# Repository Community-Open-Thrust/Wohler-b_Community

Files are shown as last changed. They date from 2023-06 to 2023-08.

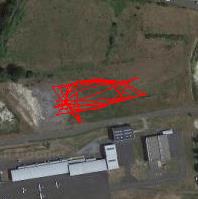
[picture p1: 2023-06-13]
Flight_Tests/logs from 03-17 to 03-24/2019-03-17 19-36-37.bin.jpg

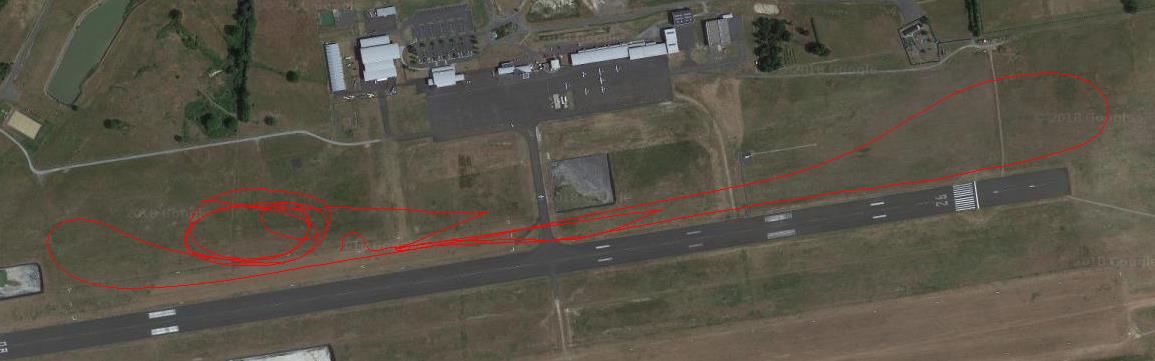
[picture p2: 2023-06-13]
Flight_Tests/logs from 03-17 to 03-24/2019-03-21 13-17-54.log.jpg

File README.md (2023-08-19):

# Wohler-b transport turbo-drone - Community Edition

This is the repository for the Community Edition Release of the community of makers from Neva Aerospace Ltd (UK) for the turbo-drone Wohler-b series for transporation.



Wohler-b series can be used with Athena-A-2ET (2stages) or Athena-A-1ET (1 stage) electric turbines (Electric Ducted Fans (EDF))

# THE LICENCE IS CERN-OHL-S (Strongly Reciprocal) 
https://ohwr.org/cern_ohl_s_v2.pdf


Any further fork and/or modification must bear the following Notice as per chapter 1.10 of Definition of the OHL-s :
"Acknowledgement of the Original Authors: Neva-Aero and the Human Team Members between 2013 and 2022 : F.M. Robert Vergnes, David Brotherton-Ratcliffe, Aleksey Zaitsevsky, Renaud-Pierre Blanpain, Anthony Gambus, Tal Stokes, Valentin Bertrand, Tomas Valaitis, Louis Fourdan, Elie de Fonclare, Frédéric Pudleitner, Gilles Coïa  "

# About using this repository
MAIN WILL NOT CHANGE.
The main of repository will be locked to the initial commit to avoid losing information. 
Please do create a new branch for a new version or create your own fork.
Please check the branch for the early or the last version of the project.

# Serialisation & History
It started in 2016-2017 with the Eole X4, followed by the Wohler-b-III-x4 (Mark 3) and then the Wohler-b-Mark-V-X8 (Wohler b mark 5).

The Eole-X4 was used for demonstration in Oct. 2017 with Thales for the French Army (STAT) at Satory Camp (France) and the Eole-X4 was then presented at the Paris Air Show 2017 at the PAS-Start-up-Aero-LAB. It ended its life at the Aero-Museum of Angers Airport. 

The Wohler-b-III-x4 (mark3) had a short life from 2017 to 2018 and the fate of the last prototype is unkown.

The Wohler-b-Mark-V-X12 (Mark5) was built between 2018 and 2019 and used for several demonstrations, among which for the French Army (STAT) were BVLOS was demonstrated using 4G and the FlyTbase cloud and UAVCast for delivery of 3Kg to 5kg package. The Wohler-b-Mark-V-X12 was presented to the Paris Air Show 2019 and the late Olivier Dassault, MP & Pilot, came to congratulates the team for the technological advance. The prototype has been dismantled at the closure of the Angers Airport operations in France.

There has been some sketches and early draft for the Wohler-D and the Wohler-b-Mark-VI-x12 but they have never been built.

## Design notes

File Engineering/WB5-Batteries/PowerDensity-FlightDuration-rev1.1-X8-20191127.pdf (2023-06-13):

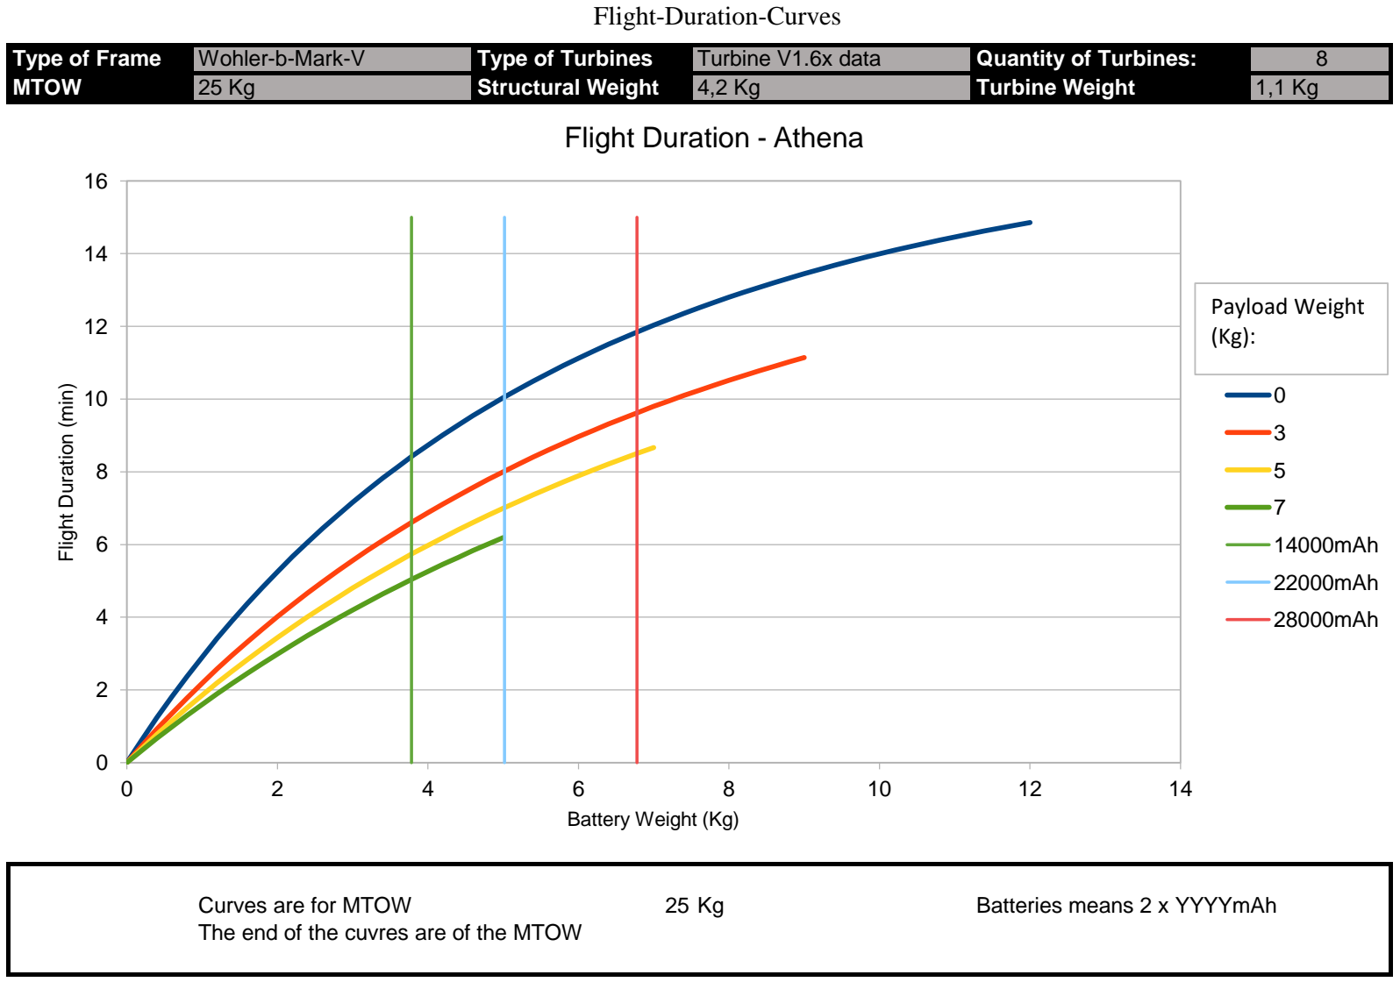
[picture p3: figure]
Flight-Duration-Curves; MTOW 25 Kg; Structural Weight 4,2 Kg; Turbine Weight 1,1 Kg; Curves are for MTOW; Batteries means 2 x YYYYmAh; The end of the cuvres are of the MTOW; Flight Duration (min); Battery Weight (Kg); Flight Duration - Athena; 14000mAh; 22000mAh; 28000mAh; Payload Weight (Kg):

Type of Frame Wohler-b-Mark-V | Type of Turbines Turbine V1.6x data | Quantity of Turbines: 8

Page 1

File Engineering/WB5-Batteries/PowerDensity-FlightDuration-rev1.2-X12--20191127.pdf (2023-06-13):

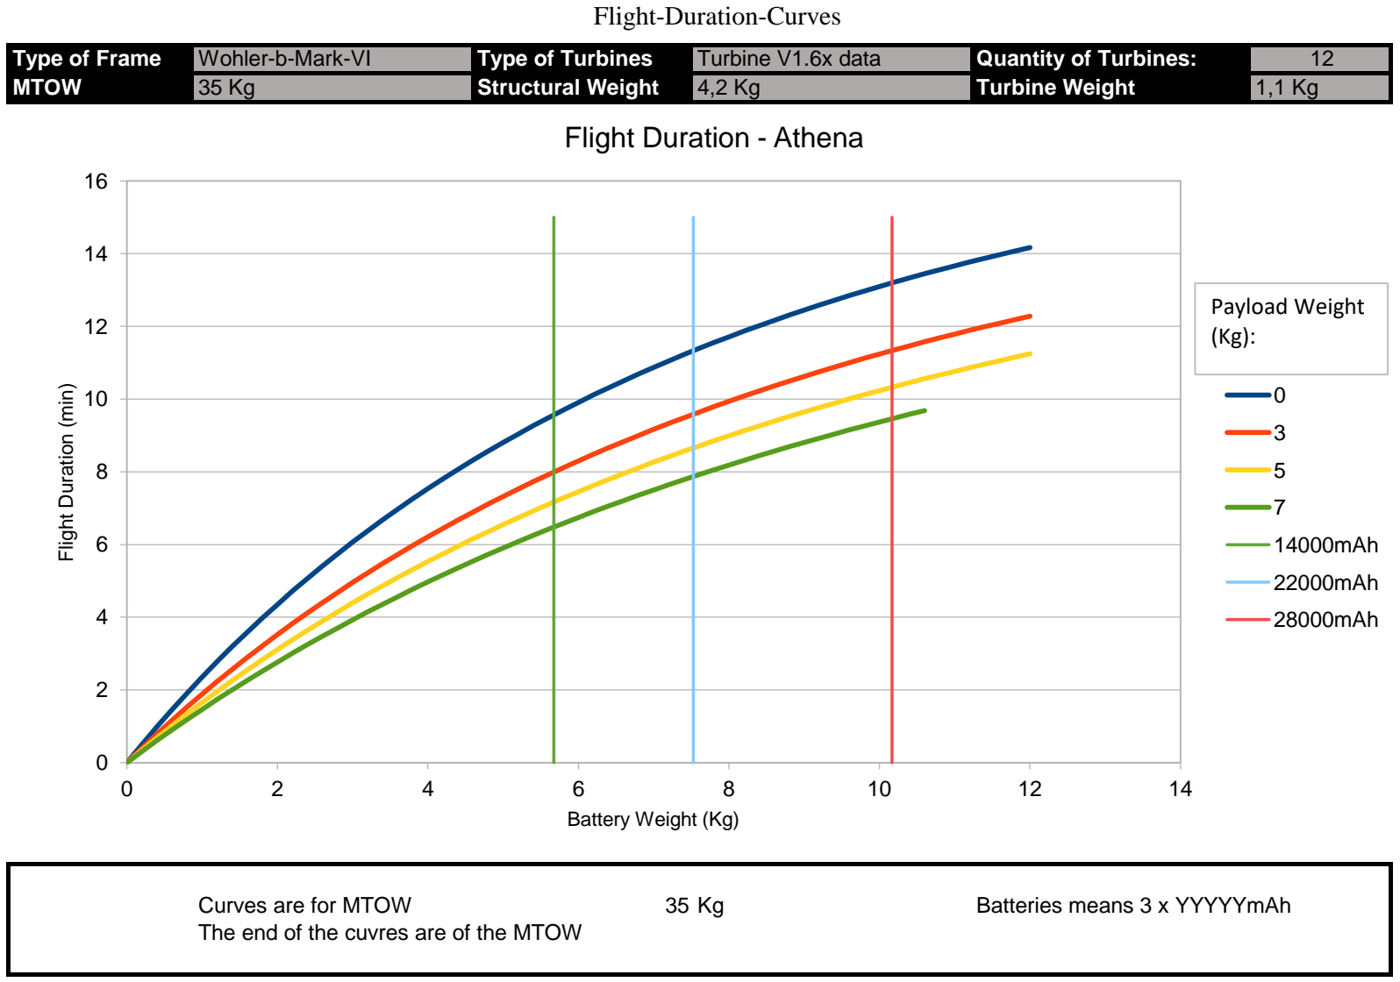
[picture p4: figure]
Flight-Duration-Curves; MTOW 35 Kg; Structural Weight 4,2 Kg; Turbine Weight 1,1 Kg; Curves are for MTOW; Batteries means 3 x YYYYYmAh; The end of the cuvres are of the MTOW; Flight Duration (min); Battery Weight (Kg); Flight Duration - Athena; 14000mAh; 22000mAh; 28000mAh; Payload Weight (Kg):

Type of Frame Wohler-b-Mark-VI | Type of Turbines Turbine V1.6x data | Quantity of Turbines: 12

Page 1

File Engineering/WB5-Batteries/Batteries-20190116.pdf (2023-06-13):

https://www.gensace.de/uav-lipo?voltage=150

S | mAH | C | Weight | Unit Price | Qty | Total mAH | Total Weight Total Price | maH/g | €/mAH
6S | 30000 | 25C | 3505 | 617,00 € | 2 | 60000 | 7010 | 1.234,00 € | 8,559201 | 0,02057 €
6S | 28000 | 25C | 3389 | 577,00 € | 2 | 56000 | 6778 | 1.154,00 € | 8,262024 | 0,02061 €
6S | 26000 | 25C | 3168 | 532,00 € | 2 | 52000 | 6336 | 1.064,00 € | 8,207071 | 0,02046 €
6S | 22000 | 25C | 2509 | 429,00 € | 2 | 44000 | 5018 | 858,00 € | 8,768434 | 0,01950 €
PLUS | 6S | 22000 | 25C | 2640 | 450,00 € | 2 | 44000 | 5280 | 900,00 € | 8,333333 | 0,02045 €
| 6S | 14000 | 25C | 1882 | 180,00 € | 4 | 56000 | 7528 | 720,00 € | 7,438895 | 0,01286 €

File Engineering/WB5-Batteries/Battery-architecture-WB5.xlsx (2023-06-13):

 | Centralized Pack* | Distributed Pack* |  | *Centralized : batteries are connected in parallel and provide energy for all EDF
Batt carac |  |  |  | *Distributed : each battery is connected to one EDF and provides energy to one EDF (only GND common)
Capacity (mAh) | 22000 | 5000
Nb of cells (S) | 6 | 6
Dicharge rate (C) | 25 | 60 | (120 burst)
Weight/unit (gr) | 2510 | 735
Nb mounted on WB5 | 2 | 8
Total Capacity (mAh) | 44000 | 40000
Max current/Athena (A) | 137.5 | 300 | (600 burst) | →We double the max current/edf, normally we would reduce the voltage drop / this value approach racing drone parameters good
Total Weight (gr) | 5020 | 5880

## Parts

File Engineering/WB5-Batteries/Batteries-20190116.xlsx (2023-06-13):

 |  |  | https://www.gensace.de/uav-lipo?voltage=150
 | S | mAH | C | Weight | Unit Price | Qty | Total mAH | Total Weight | Total Price | maH/g | €/mAH
 | 6S | 30000 | 25C | 3505 | 617.00 € | 2 | 60000 | 7010 | 1234.00 € | 8.559201141 | 0.02057 €
 | 6S | 28000 | 25C | 3389 | 577.00 € | 2 | 56000 | 6778 | 1154.00 € | 8.262024196 | 0.02061 €
 | 6S | 26000 | 25C | 3168 | 532.00 € | 2 | 52000 | 6336 | 1064.00 € | 8.207070707 | 0.02046 €
 | 6S | 22000 | 25C | 2509 | 429.00 € | 2 | 44000 | 5018 | 858.00 € | 8.768433639 | 0.01950 €
PLUS | 6S | 22000 | 25C | 2640 | 450.00 € | 2 | 44000 | 5280 | 900.00 € | 8.333333333 | 0.02045 €
 | 6S | 14000 | 25C | 1882 | 180.00 € | 4 | 56000 | 7528 | 720.00 € | 7.438894793 | 0.01286 €

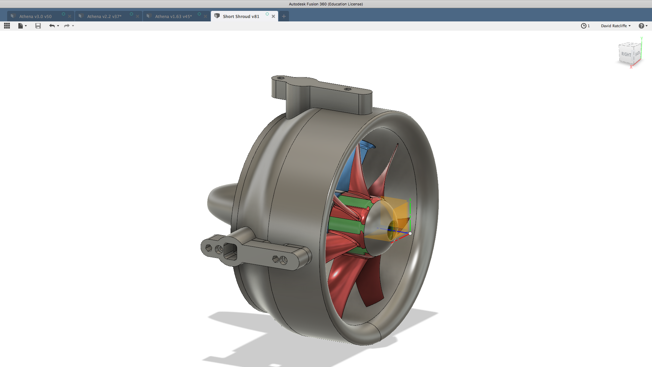
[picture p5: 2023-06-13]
Engineering/CAD_3D-Parts-WB5/Adapter-V1-V2/Screen Shot 2019-03-01 at 02.17.48(1).png

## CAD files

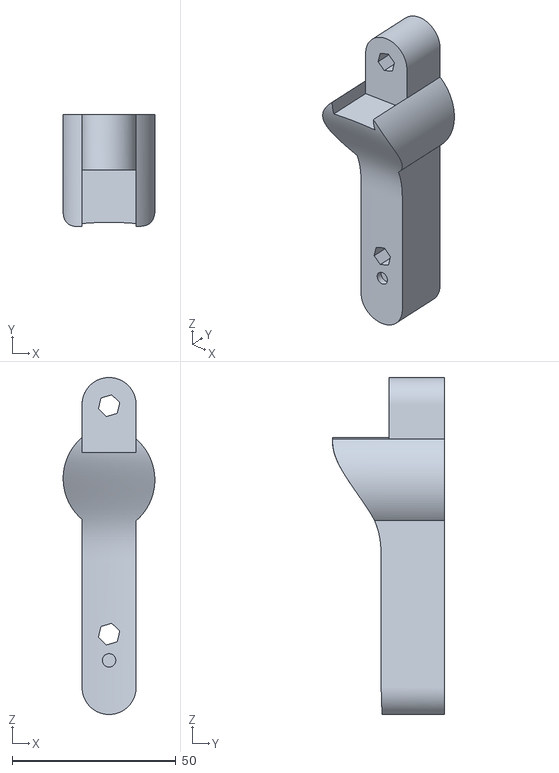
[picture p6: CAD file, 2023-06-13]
Engineering/CAD_3D-Parts-WB5/Adapter-V1-V2/V164 Adaptor2.stl
28.0 x 34.2 x 102.7

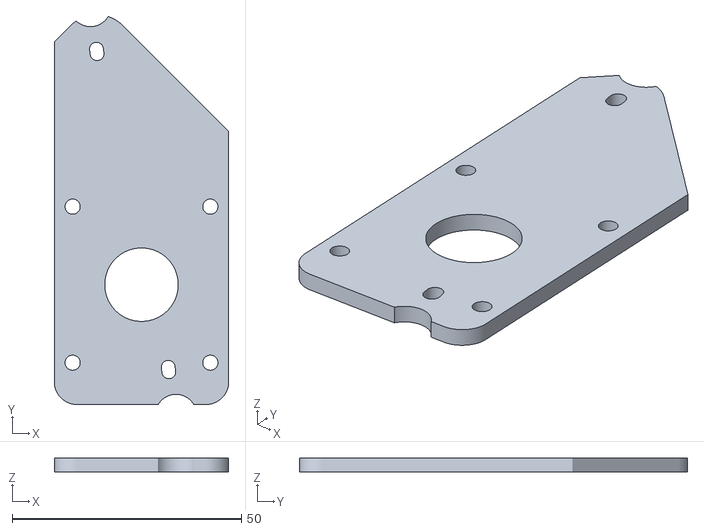
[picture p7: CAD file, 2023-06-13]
Engineering/CAD_3D-Parts-WB5/Plate B12-WB5-20181212.stl
38.0 x 84.5 x 3.00

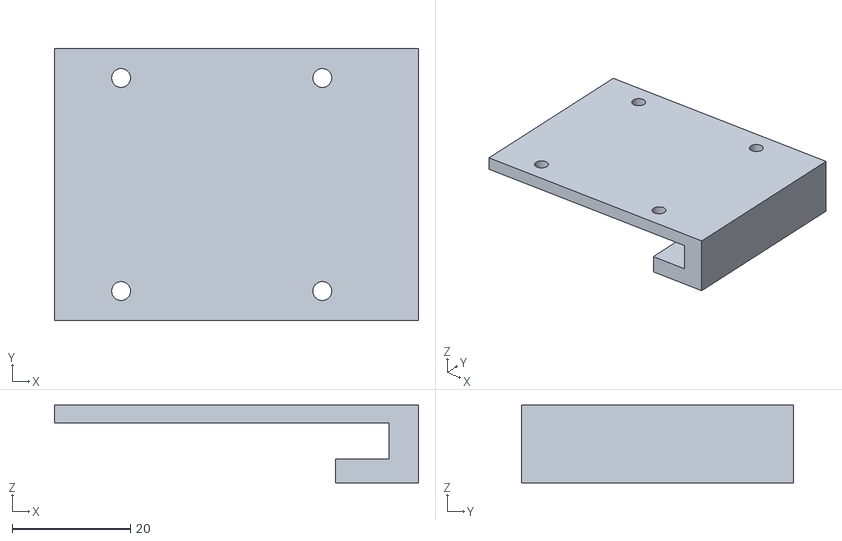
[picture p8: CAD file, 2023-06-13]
Engineering/WB5-AssemblingManual/LDG-Drill-Tool.stl
61.5 x 46.0 x 13.1

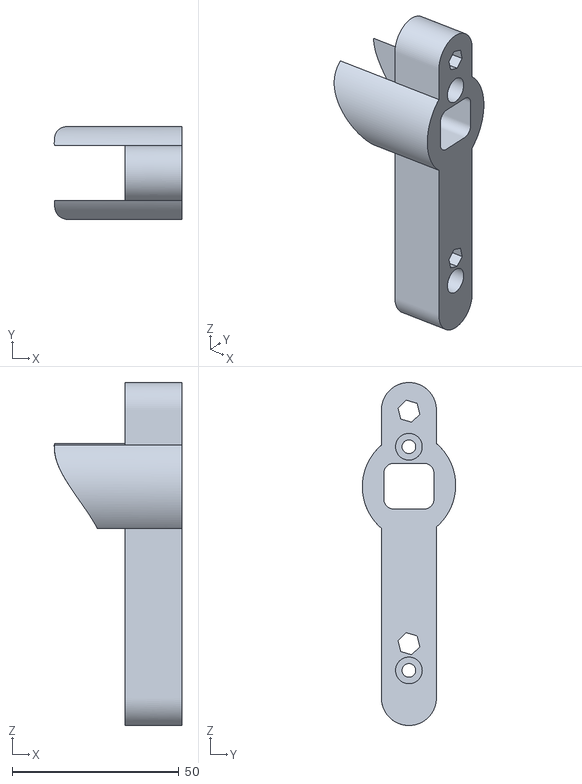
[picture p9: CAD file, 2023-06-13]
Engineering/CAD_3D-Parts-WB5/Adapter-V1-V2/V164 Adaptor1.stl
38.2 x 28.0 x 102.7

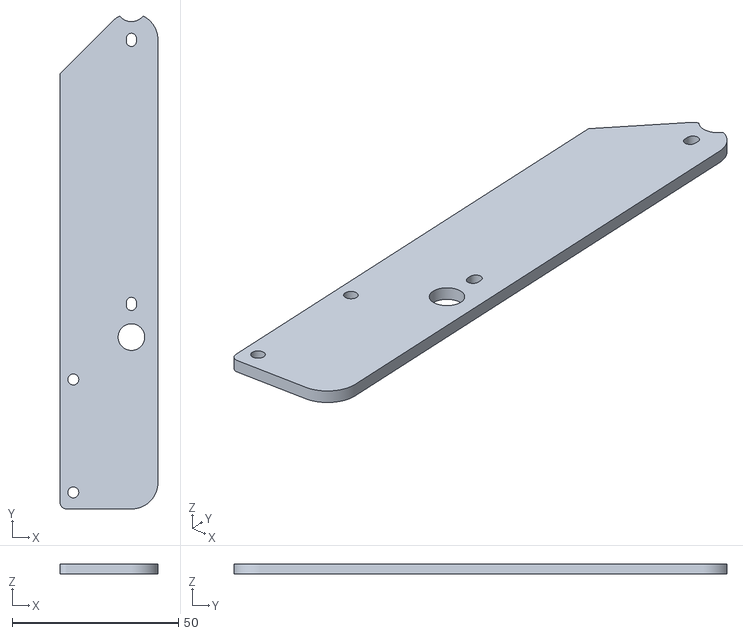
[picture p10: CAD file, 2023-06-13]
Engineering/CAD_3D-Parts-WB5/Plate E12-WB5-20181212.stl
29.5 x 148.5 x 3.00

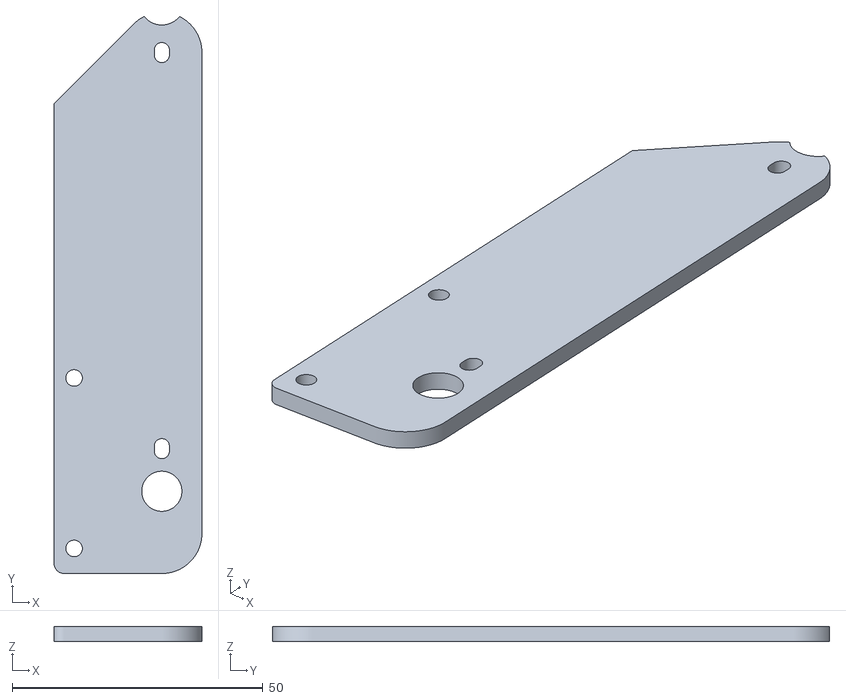
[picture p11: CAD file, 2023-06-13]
Engineering/CAD_3D-Parts-WB5/Plate D12-WB5-20181212.stl
29.5 x 111.1 x 3.00

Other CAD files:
Engineering/CAD_3D-Parts-WB5/Plate B12 - 2D drawing.dwg
Engineering/CAD_3D-Parts-WB5/Plate D12 - 2D drawing.dwg
Engineering/CAD_3D-Parts-WB5/Plate E12 - 2D drawing.dwg
Engineering/CAD_3D-Parts-WB5/mark-V-Carbon-20181120-rev2-AZ.dwg
Engineering/CAD_3D-Parts-WB5/Plate C12 - 2D drawing.dwg
Engineering/CAD_3D-Parts-WB5/Wohler-b-mark-V-x8-Carbon.dwg

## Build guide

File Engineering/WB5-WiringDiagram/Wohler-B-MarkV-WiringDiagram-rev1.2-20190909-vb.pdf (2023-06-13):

# Wohler-b-MarkV-

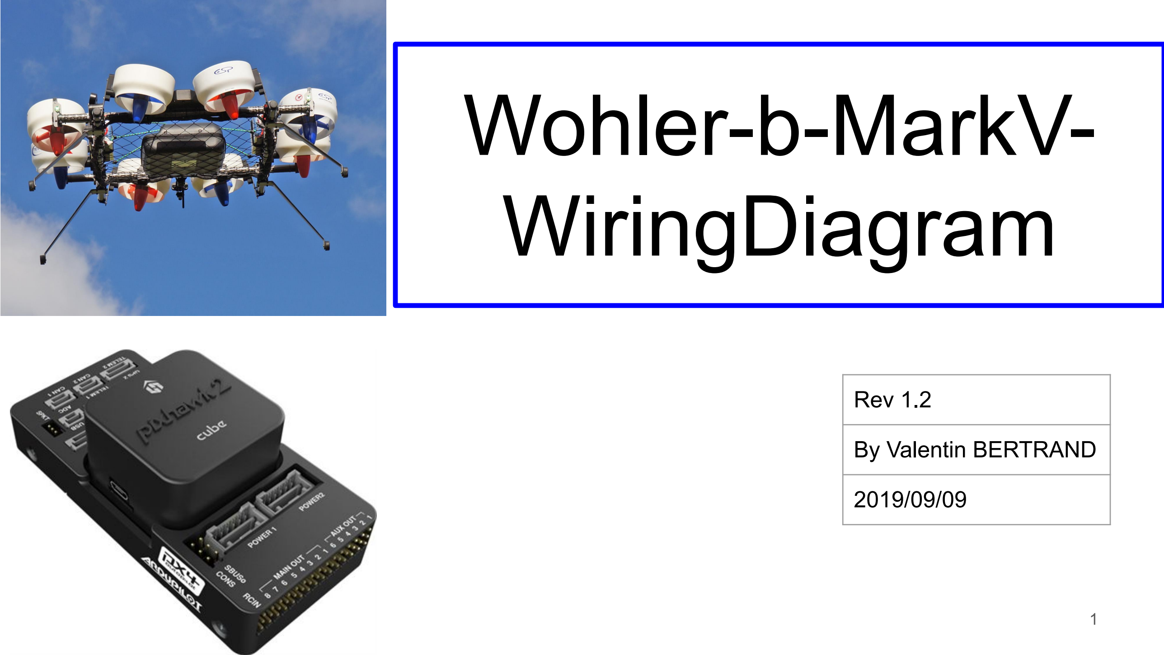
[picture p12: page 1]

# WiringDiagram

Rev 1.2

By Valentin BERTRAND

2019/09/09

# Full Main Circuit (PixHawk Circuit)

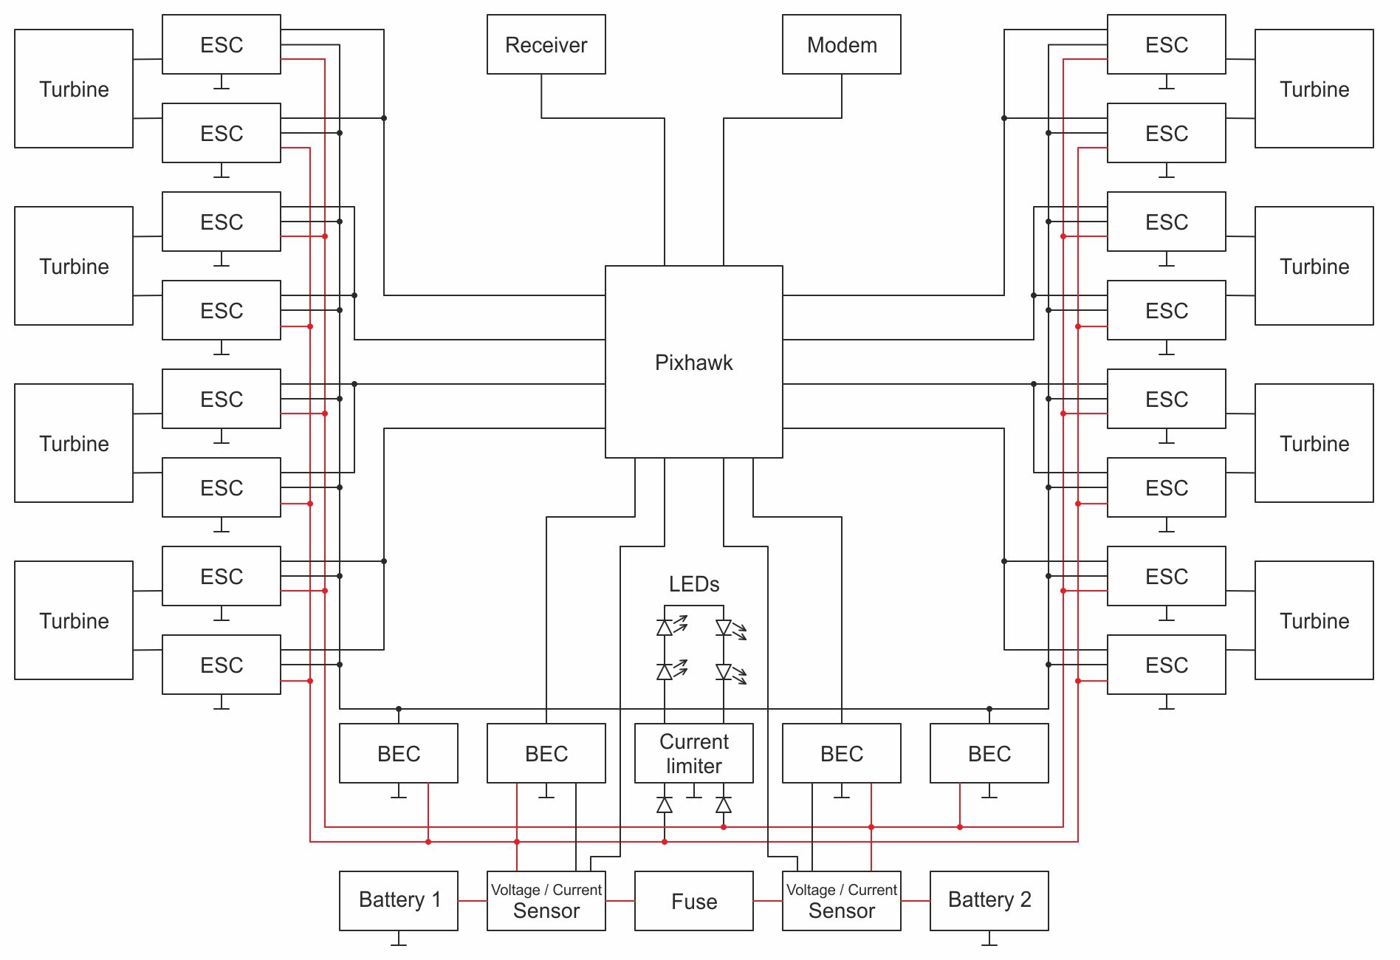
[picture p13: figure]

# Auxiliary Circuit (Rasp, FPV TX...)

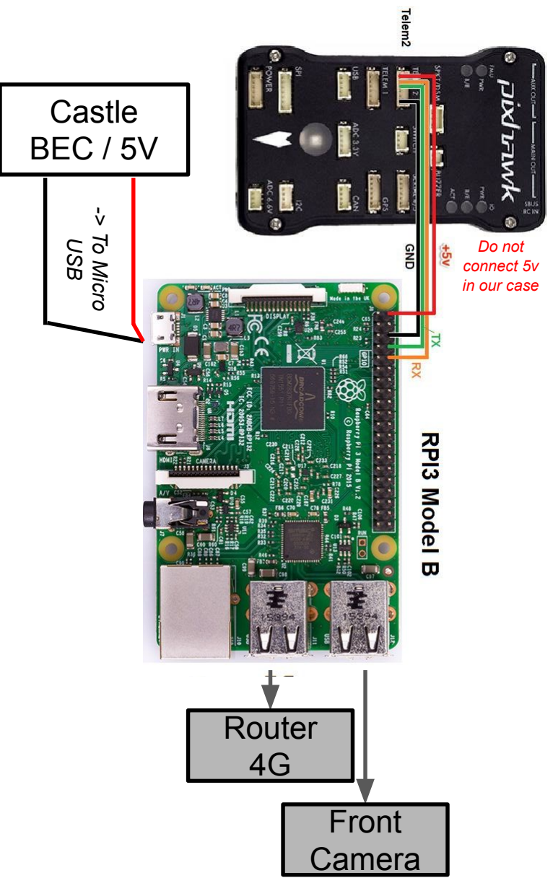
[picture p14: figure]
Router 4G; Front Camera; Castle BEC / 5V -> To Micro USB; Do not connect 5v in our case

UAS
22+
/12V

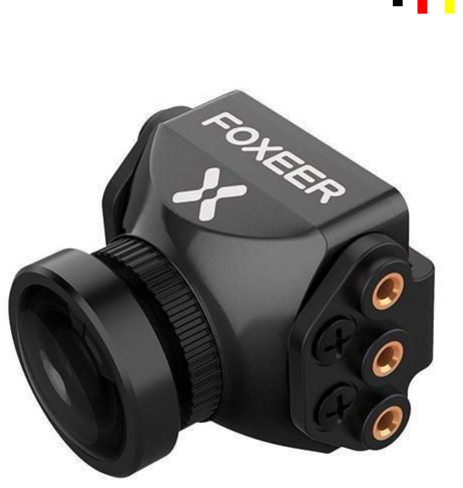
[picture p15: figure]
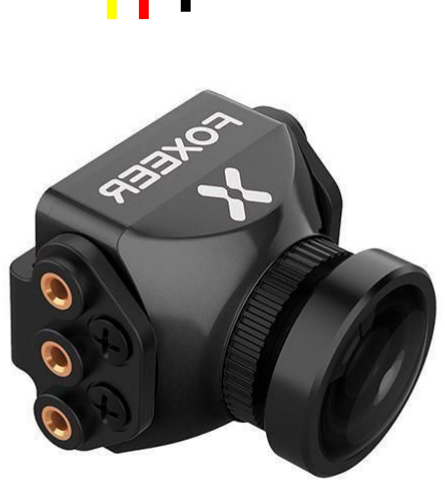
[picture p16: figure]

Front camera | Back camera

Video transmission diagram :

TX TS832 | TX TS832

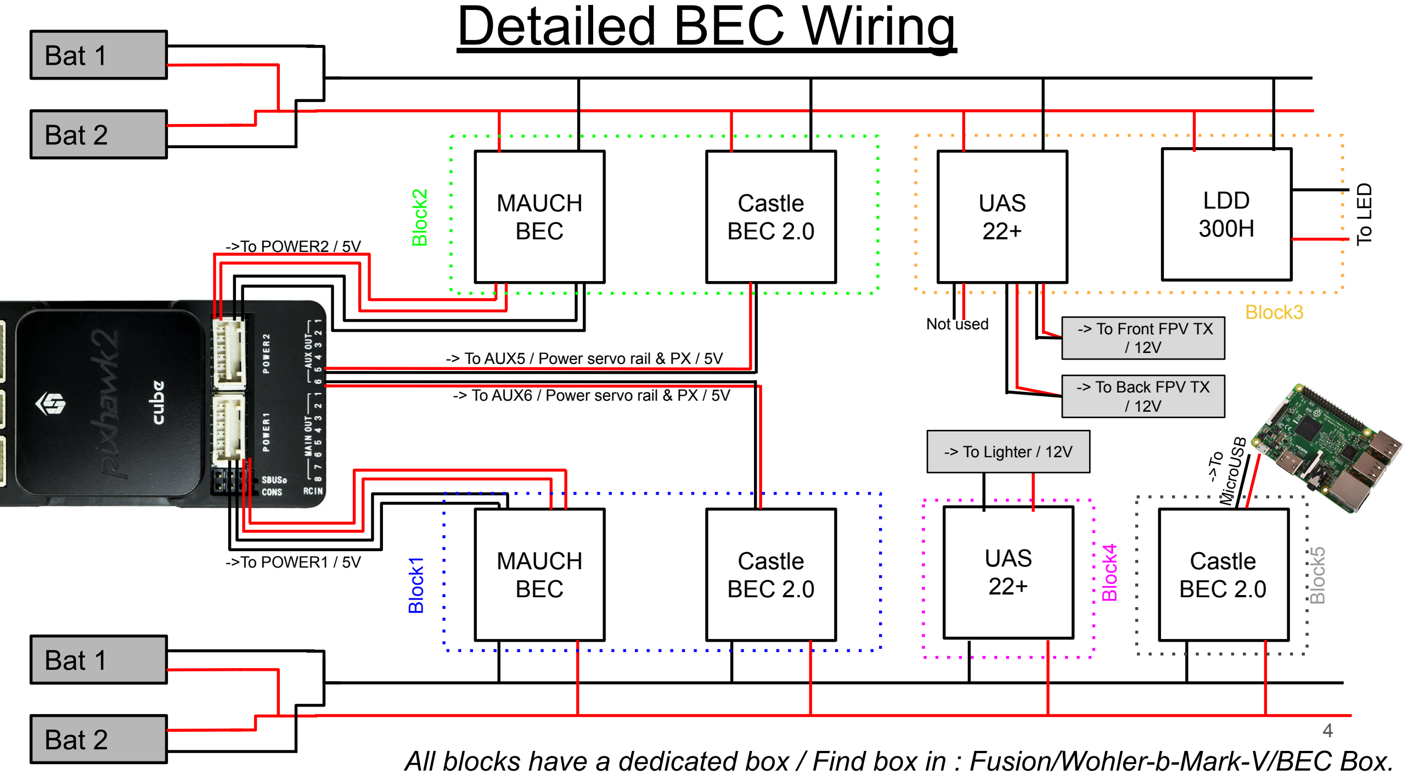
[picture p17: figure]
Detailed BEC Wiring; MAUCH BEC; Castle BEC 2.0; UAS 22+; LDD 300H; Bat 2; Bat 1; To LED; Not used; -> To Back FPV TX / 12V; -> To AUX5 / Power servo rail & PX / 5V; -> To AUX6 / Power servo rail & PX / 5V; ->To POWER2 / 5V; ->To POWER1 / 5V; Castle; BEC 2.0; MicroUSB; Block1 Block2; Block5; -> To Front FPV TX / 12V; Block3; Block4; -> To Lighter / 12V

All blocks have a dedicated box / Find box in : Fusion/Wohler-b-Mark-V/BEC Box.

# OEM / Electromagnetic Wave protection Part1

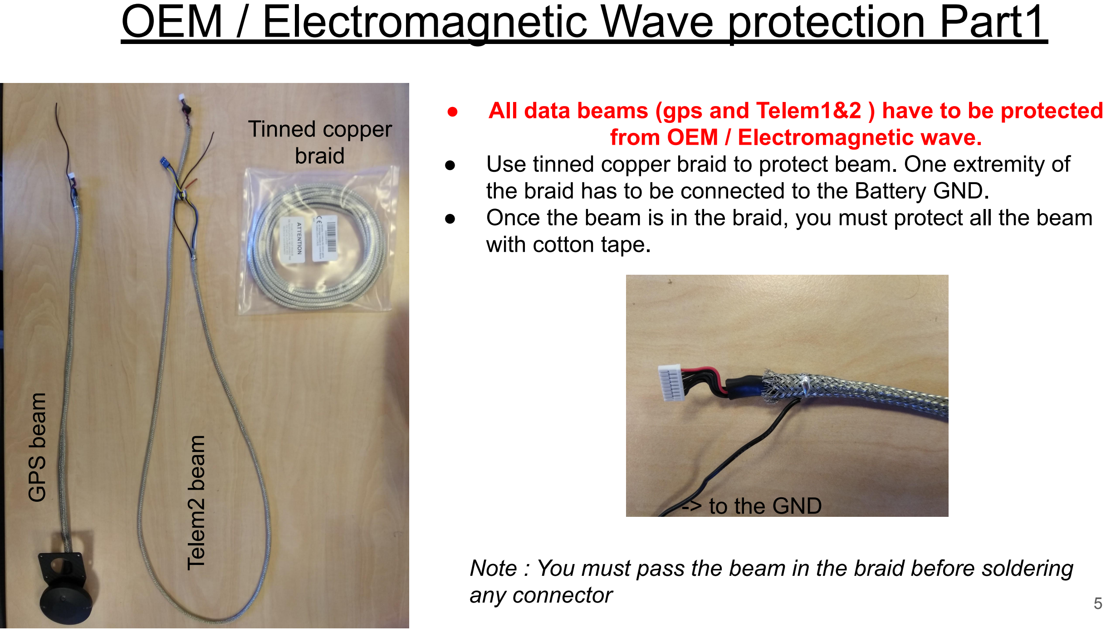
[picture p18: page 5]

GPS beam

Telem2 beam

Tinned copper
braid
- All data beams (gps and Telem1&2 ) have to be protected from OEM / Electromagnetic wave.
- Use tinned copper braid to protect beam. One extremity of the braid has to be connected to the Battery GND.
- Once the beam is in the braid, you must protect all the beam with cotton tape.

-> to the GND

Note : You must pass the beam in the braid before soldering any connector

# OEM / Electromagnetic Wave protection Part2

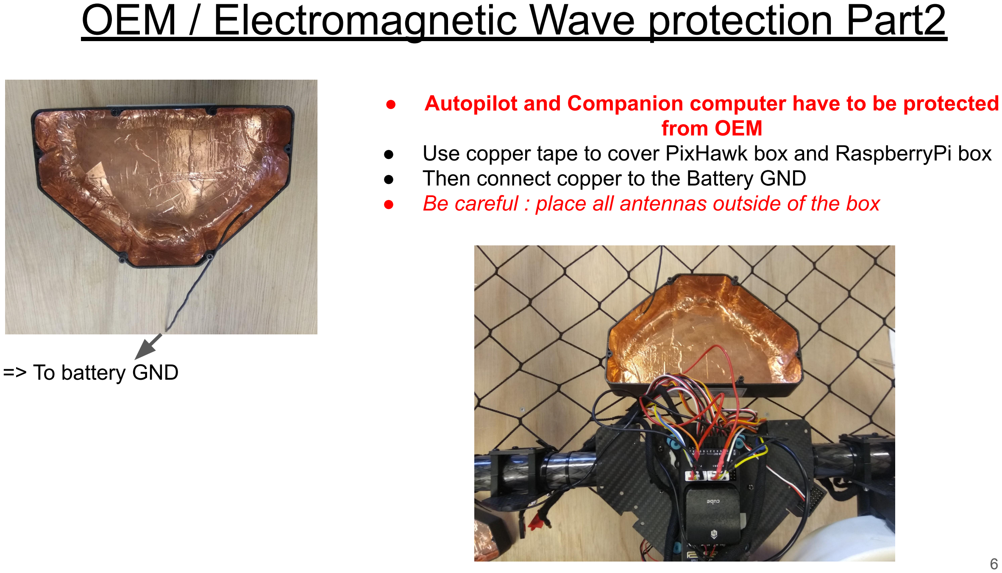
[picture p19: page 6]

- Autopilot and Companion computer have to be protected from OEM
- Use copper tape to cover PixHawk box and RaspberryPi box
- Then connect copper to the Battery GND
- Be careful : place all antennas outside of the box

=> To battery GND

# OEM / Electromagnetic Wave protection Part3

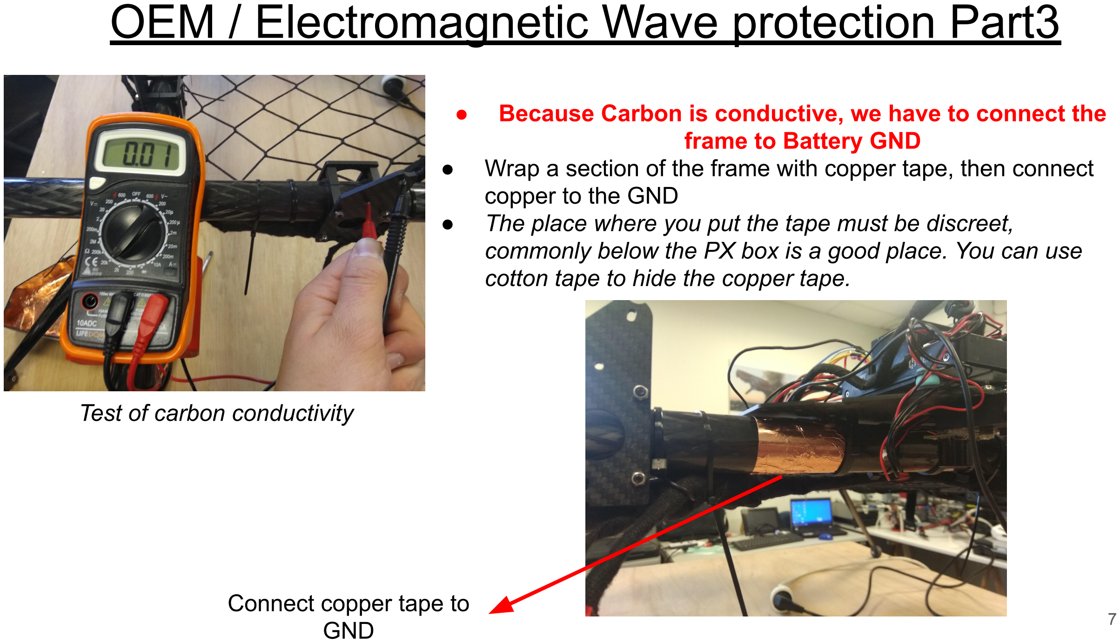
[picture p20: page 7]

- Because Carbon is conductive, we have to connect the frame to Battery GND
- Wrap a section of the frame with copper tape, then connect copper to the GND
- The place where you put the tape must be discreet, commonly below the PX box is a good place. You can use cotton tape to hide the copper tape.

Test of carbon conductivity

Connect copper tape to
GND

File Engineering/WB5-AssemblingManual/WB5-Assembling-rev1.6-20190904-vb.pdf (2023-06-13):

# Wohler Mark V -Delivery Drone

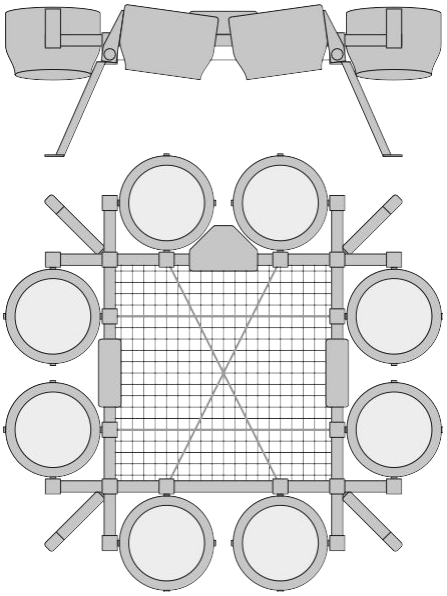
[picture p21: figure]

Technical Specs :
- Frame was designed to fly with 8 turbines Athena V1.64
- Power source - two batteries Li-Po, 6S, 22Ah, 25C, 2500g each.
- Autopilot - Pixhawk2 Cube
- Payload up to 10 kg, 550x540x220mm (cabin luggage size)
- Size of the drone - 116x117x43cm
- Mass of the frame only - 2,3kg
- Frame with wiring and avionics - 3,4kg
- Batteries - 5,1kg
- Turbines - 1,15kg each, 9,2kg - eight turbines.
- RTF mass - 17,7kg
- Safe thrust of Athena 1.64 turbine - 30N (20V on ESC, 40A)
- Total thrust - up to 300N on a full battery

rev 1.6

By Valentin BERTRAND

2019/08/21

# I) Assembling LDG (1/2)

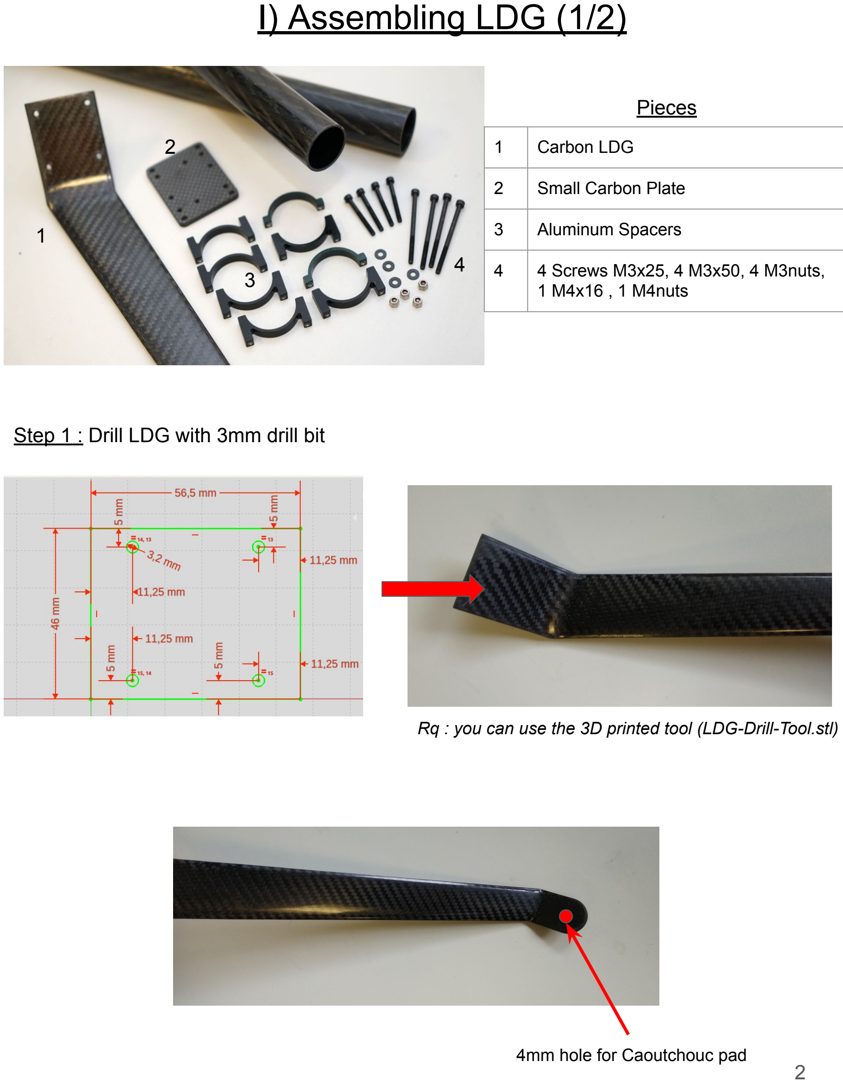
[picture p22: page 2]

1 | Carbon LDG
2 | Small Carbon Plate
3 | Aluminum Spacers
4 | 4 Screws M3x25, 4 M3x50, 4 M3nuts, 1 M4x16 , 1 M4nuts

Pieces

1

2

3

4

Step 1 : Drill LDG with 3mm drill bit

Rq : you can use the 3D printed tool (LDG-Drill-Tool.stl)

4mm hole for Caoutchouc pad

# I) Assembling LDG (2/2)

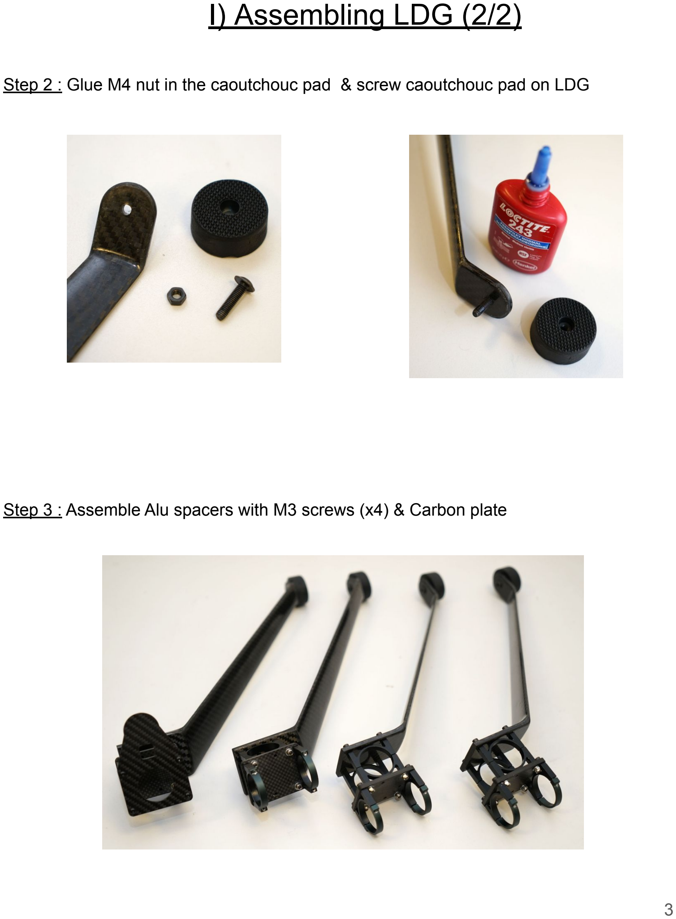
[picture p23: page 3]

Step 2 : Glue M4 nut in the caoutchouc pad & screw caoutchouc pad on LDG
Step 3 : Assemble Alu spacers with M3 screws (x4) & Carbon plate

# II ) Assembling Turbine Holder 1

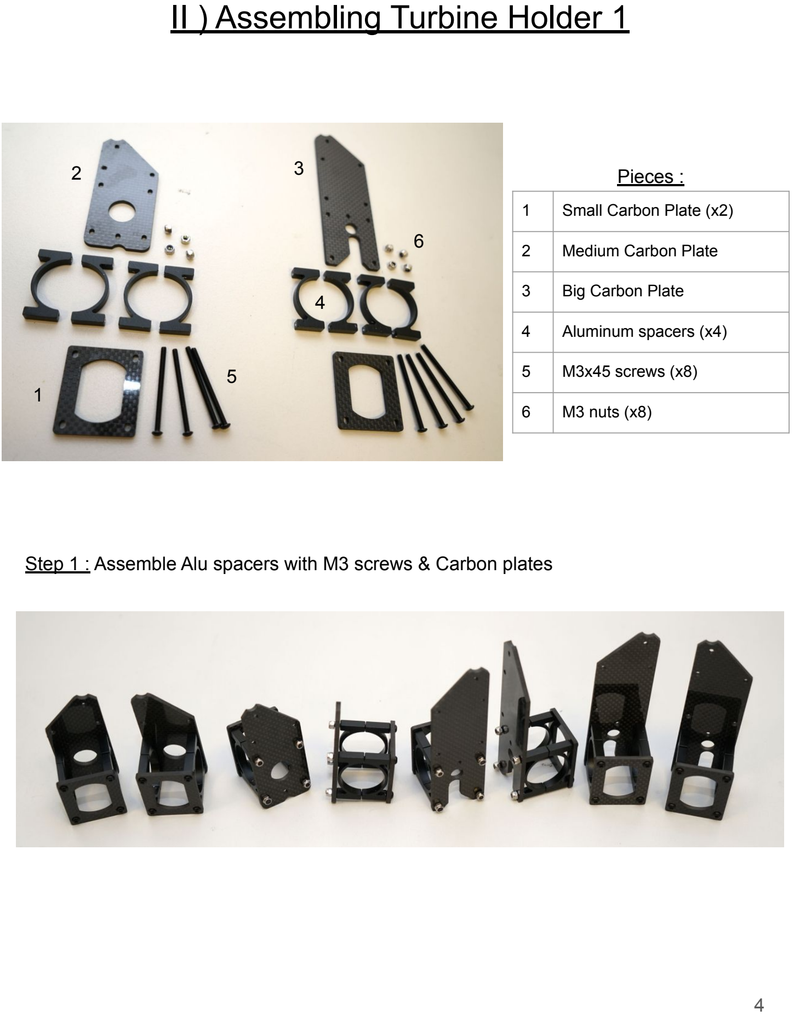
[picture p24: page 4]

1 | Small Carbon Plate (x2)
2 | Medium Carbon Plate
3 | Big Carbon Plate
4 | Aluminum spacers (x4)
5 | M3x45 screws (x8)
6 | M3 nuts (x8)

Pieces :

1

2 | 3

4

5

6

Step 1 : Assemble Alu spacers with M3 screws & Carbon plates

# III ) Assembling Turbine Holder 2

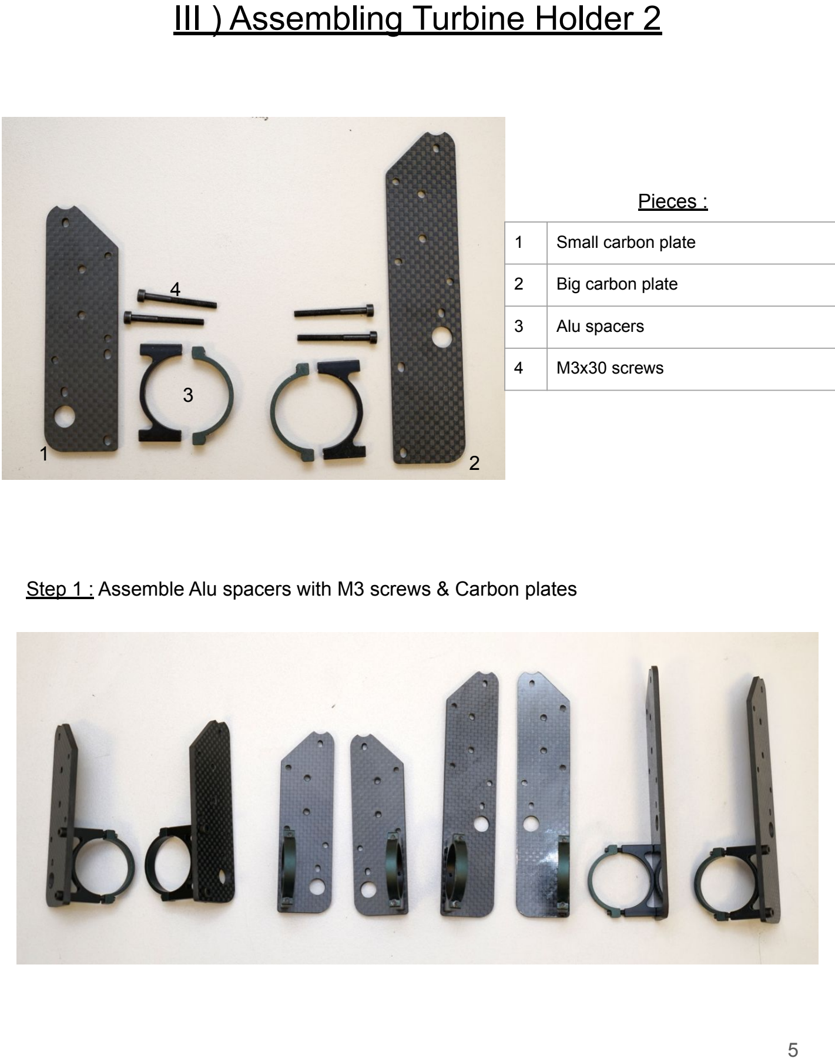
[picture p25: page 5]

Step 1 : Assemble Alu spacers with M3 screws & Carbon plates
1 | Small carbon plate
2 | Big carbon plate
3 | Alu spacers
4 | M3x30 screws

Pieces :

1
2

3

4

# IV ) Assembling PX & Battery Holder

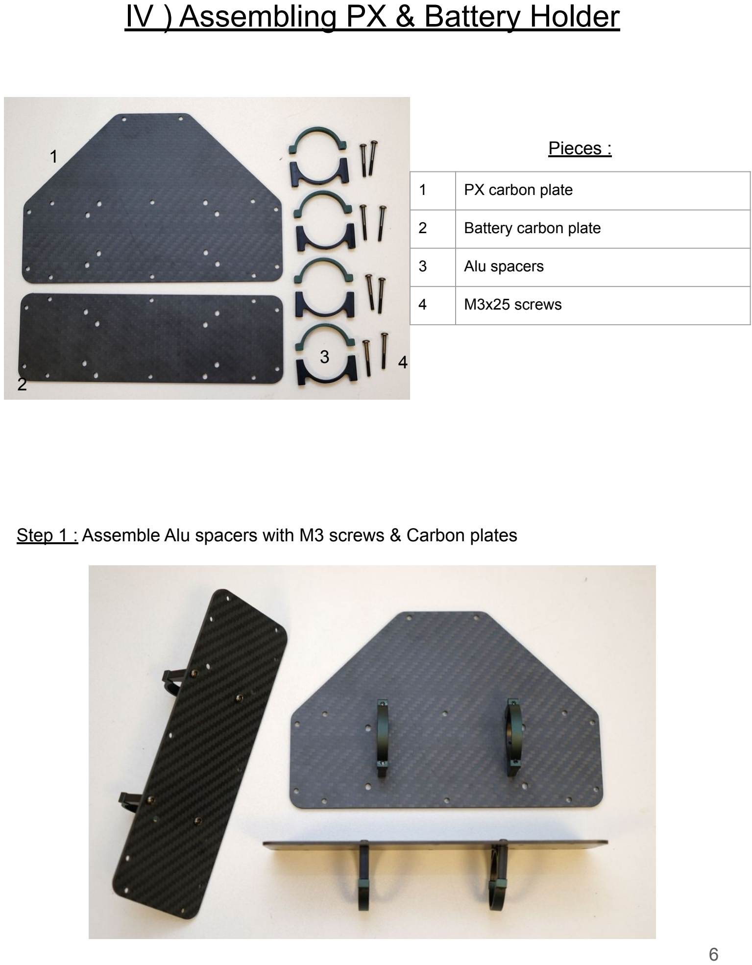
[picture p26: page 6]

1 | PX carbon plate
2 | Battery carbon plate
3 | Alu spacers
4 | M3x25 screws

Pieces :

Step 1 : Assemble Alu spacers with M3 screws & Carbon plates

1

2

3 | 4

# V ) Assembling Frame

Step 1 : Assemble Pieces previously mounted (I to IV) on carbon tubes

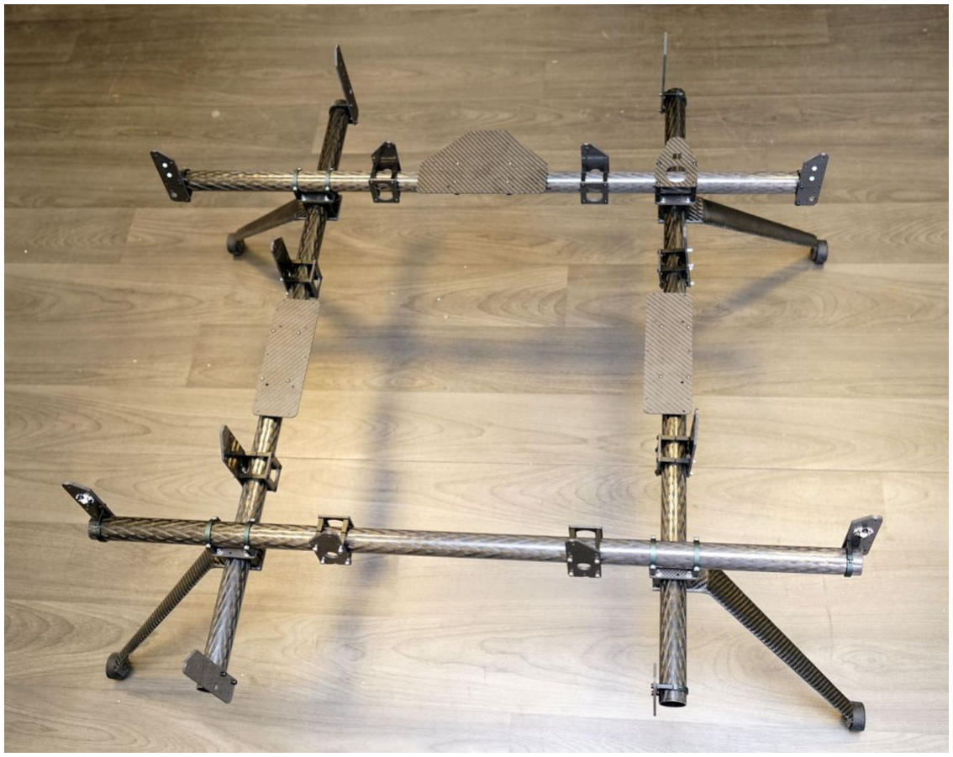
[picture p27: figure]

➔ | Symmetrical design
➔ | Attach the turbine to set proper distance between mounts.

# VI ) Mounting Nylon mesh

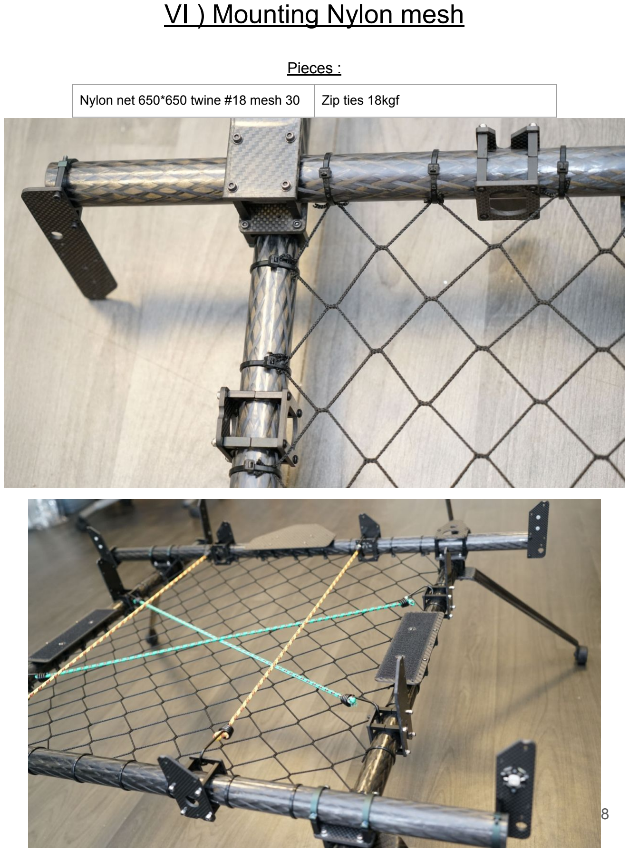
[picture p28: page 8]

Nylon net 650*650 twine #18 mesh 30 Zip ties 18kgf

Pieces :

# VII ) Wiring (1/3)

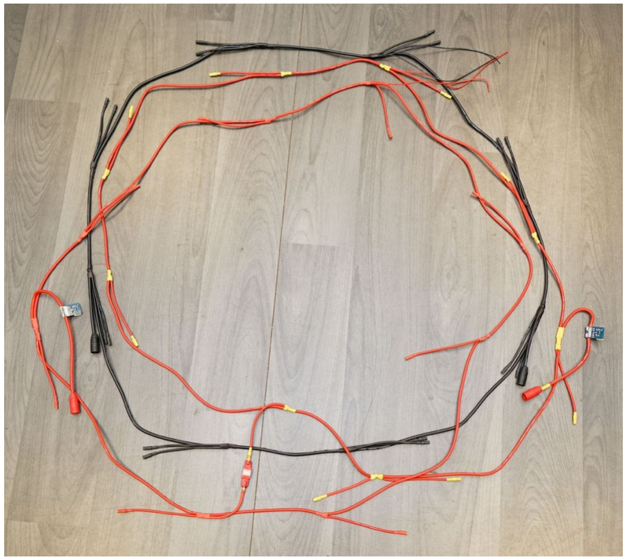
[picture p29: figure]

Power harness :
- Perimeter : 240cm
- Black 10AWG
- Red 12AWG
- Fuse
- Motor Connectors

# BEFORE WIRING SEE FULL WIRING DIAGRAM

:

In Dropbox : NPC-A024-A-B-Mark-V/Eng_Wohler-b-Mark-V-X8_…ineering /WB5-WiringDiagram/Wohler-B-MarkV-WiringDiagram-rev1.0-20190821-vb.pptx

# VII ) Wiring (2/3)

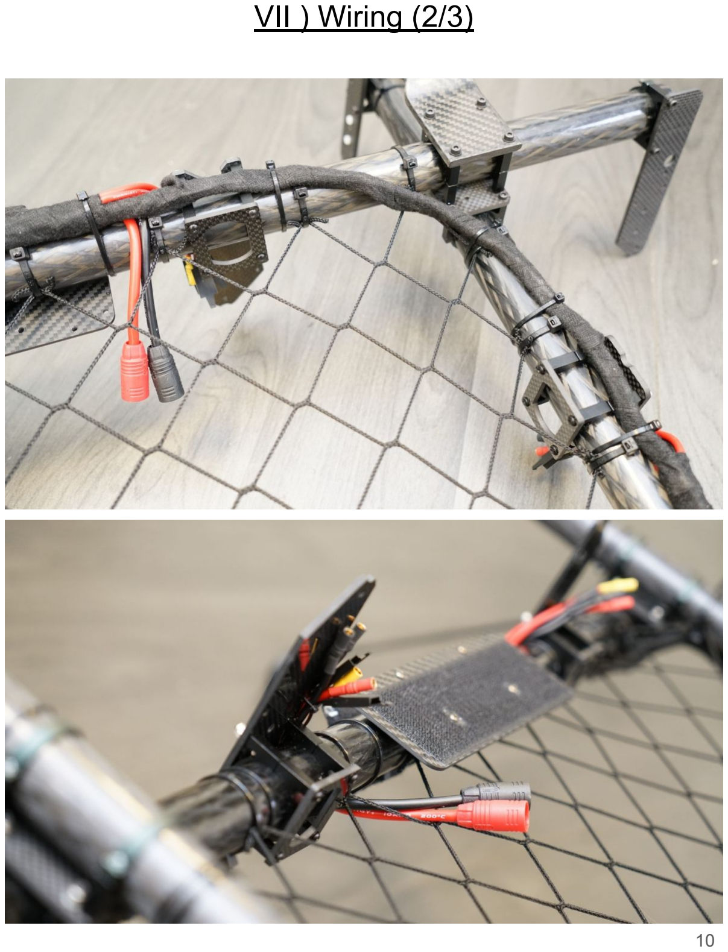
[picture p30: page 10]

# VII ) Wiring (3/3)

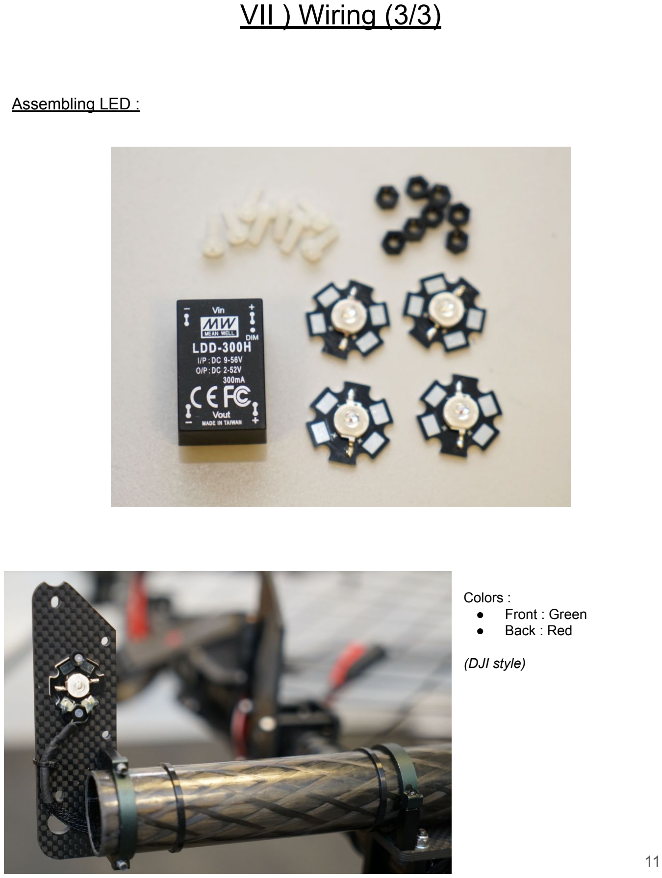
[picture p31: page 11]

Assembling LED :

Colors :
- Front : Green
- Back : Red

(DJI style)

# VIII ) Mounting Turbines

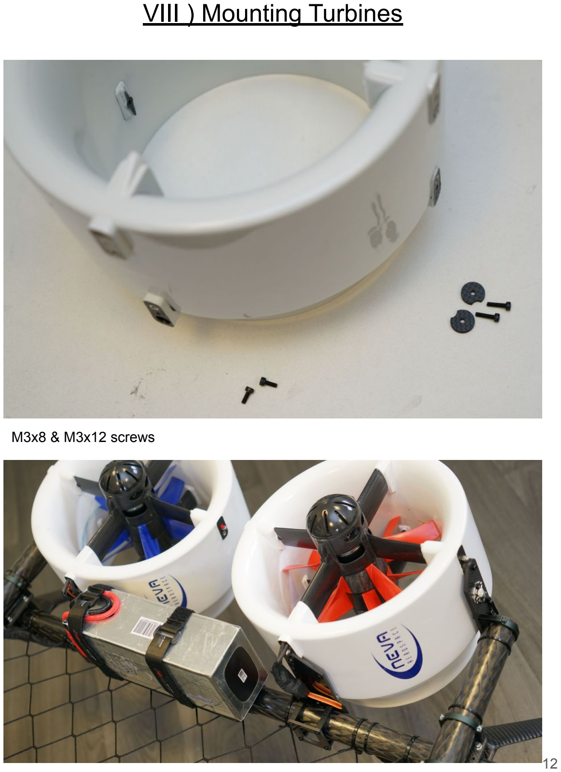
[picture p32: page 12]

M3x8 & M3x12 screws

# Final Result

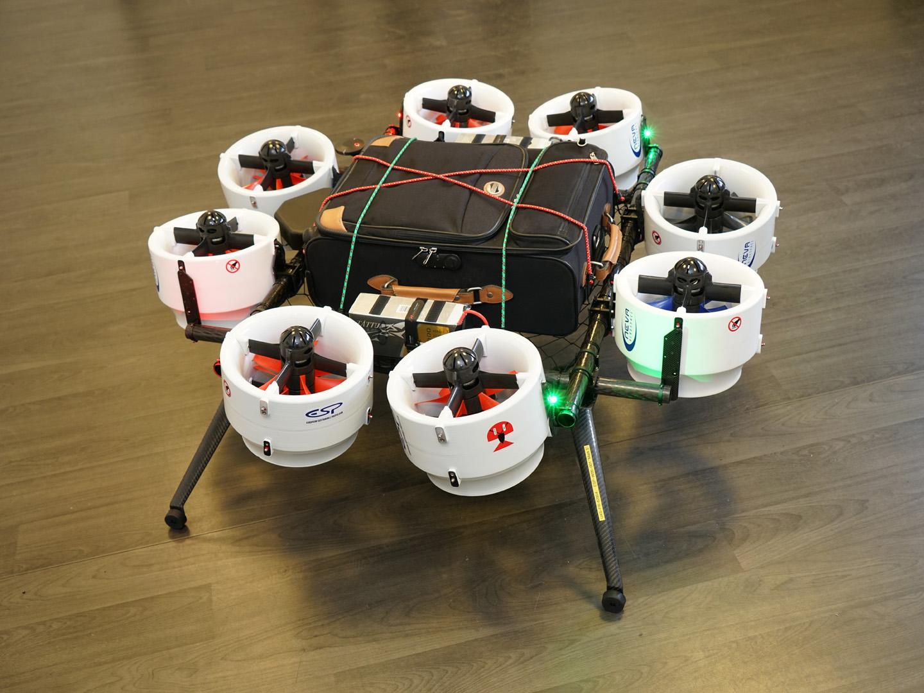
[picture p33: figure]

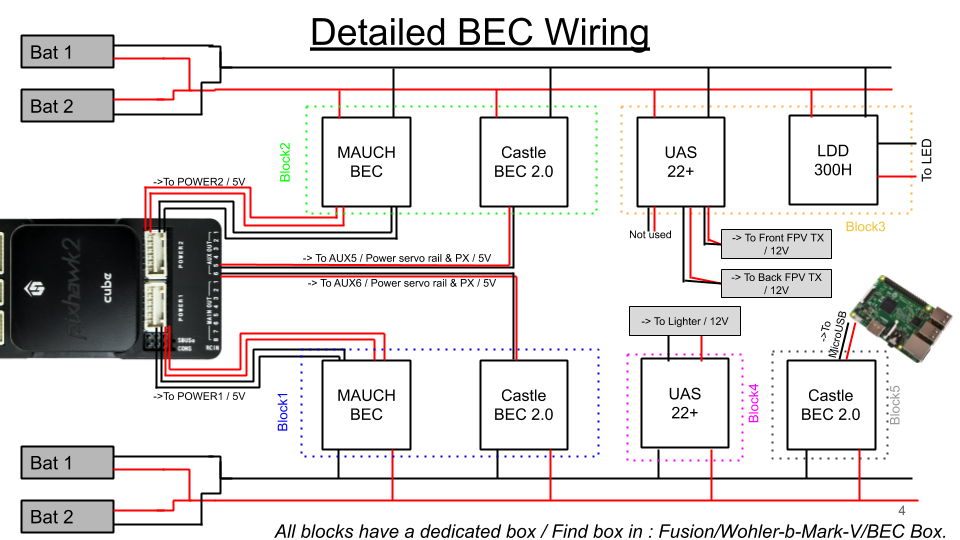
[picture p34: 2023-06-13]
Engineering/WB5-WiringDiagram/Detailed-BEC-WIRING.png

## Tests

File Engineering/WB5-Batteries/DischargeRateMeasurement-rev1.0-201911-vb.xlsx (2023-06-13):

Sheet: header
Engineer | VB
Date | 2019-11-29
rev | 1.0

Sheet: Discharge-Rate
 | Turbine | Motors | Moto NB | Max A / motor | Total Max A |  |  | Calculations from : | http://jj604.com/LiPoTool/
WB5 carac | V1.65 | MN4010-475kv | 16 | 30 | 480 |  |  | Charger used for internal Ω : | GTP-XDRIVE607
Tattu 6S 22000mAh 25C (SN : ESP-BAT-6S-004) |  |  |  |  |  |  |  | IMPORTANT NOTE :
Nb of batt to fly : |  | 2 |  |  |  |  |  | These calculations remain true for any tattu pack 22000mAh 25C (4S-6S-8S…)
Batt voltage | Batt % | Volt/Cell | Measure | Internal R (mΩ) | Max A | True C rate | Total Amp available
22.2 | 25 | 3.7 | Max | 10 | 115 | 5.227272727 | 230
 |  |  | Min | 3 | 210 | 9.545454545 | 420
24 | 75 | 4 | Max | 2 | 257 | 11.68181818 | 514
 |  |  | Min | 1 | 360 | 16.36363636 | 720
Note : this battery has a damaged cell, IT stays at 10mΩ even after charging
Gens 5000mAh 60C (SN : NEVA-BAT-6S-001)
Nb of batt to fly : |  | 8
Batt voltage | Batt % | Volt/Cell | Measure | Internal R (mΩ) | Max A | True C rate | Total Amp available
23.1 | 40 | 3.85 | Max | 10 | 55 | 11 | 440
 |  |  | Min | 7 | 65 | 13 | 520
24 | 75 | 4 | Max | 7 | 65 | 13 | 520
 |  |  | Min | 4 | 87 | 17.4 | 696
Note : this battery has a damaged cell, IT stays at 9mΩ even after charging

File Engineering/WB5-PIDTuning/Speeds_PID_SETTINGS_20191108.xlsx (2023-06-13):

FOR DRONE : WB5-0001 | MISSION TURBO-DRONE SPEEDS
 | TO RESPECT ACCORDING TO WIND GUST
Max speed (m/s) | 12
Commercial Speed (m/s) | 5 to 8
Wind Speed (m/s) | 0-3 | 4-6 | 7-9 | 10-12 | PID (PYAW=2) |  | WB5-0001/V1.645 - 20190811
Wind Speed(Knot) | 0-6 | 8-12 | 13-17 | 19-23
Drone misison speed with payload (m/s) | 10 | 8 | 6 | 5
Yaw Speed (ATC_SLEW __YAW) and (cdg/s) with payload | 2000 | 1600 | 1300 | 1000
ATC_ACCEL_Y_MAX) (cdeg/s/s) | never EVER exceed 9000 - Use 4000 as standard
Drone mission speed without payload (m/) | 12 | 10 | 8 | 6
Yaw Speed (ATC_SLEW__YAW) (cdg/s) without payload (Zero payload) | 3000 | 2500 | 2000 | 1600 | ATC_INPUT_TC | 0.2 | (ou 0,5)
NO FLY BEYOND WIND GUST 23 KNOT ( 12m/s)
CHECK METAR BEFORE MISSION FLIGHT

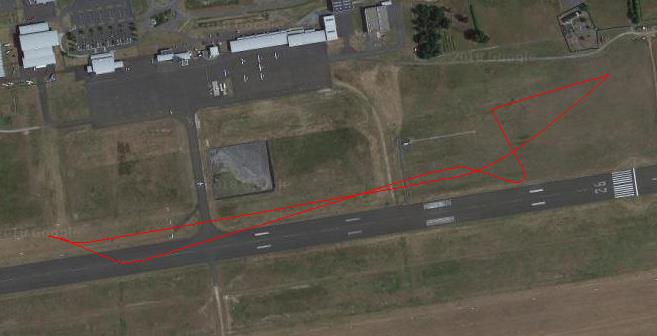
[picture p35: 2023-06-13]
Flight_Tests/logs from 03-17 to 03-24/2019-03-18 12-25-27.log.jpg

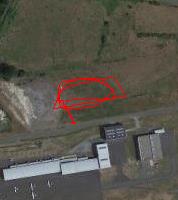
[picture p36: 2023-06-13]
Flight_Tests/logs from 03-17 to 03-24/2019-03-17 19-23-25.bin.jpg

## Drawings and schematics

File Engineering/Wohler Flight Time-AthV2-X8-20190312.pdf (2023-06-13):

## Flight Time (Mins)

# Wohler-x8 v2 Time/Weight Plot

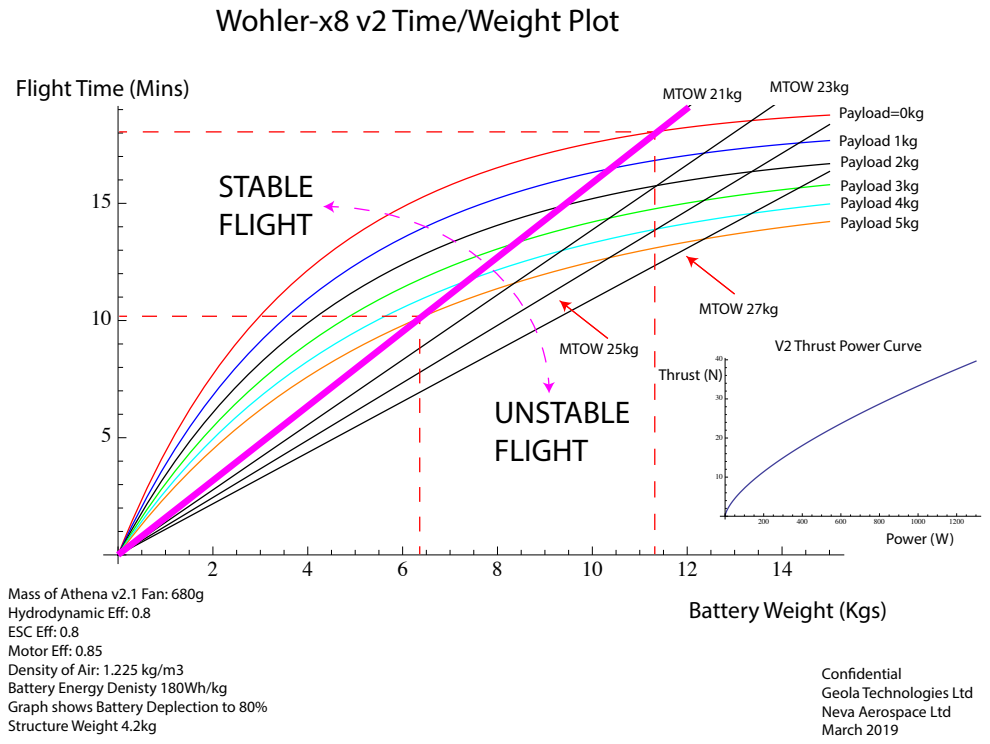
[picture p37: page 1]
Payload=0kg; Payload 1kg Payload 2kg Payload 3kg Payload 4kg Payload 5kg; MTOW 21kg; MTOW 23kg; MTOW 25kg; MTOW 27kg; 40 Thrust (N); Power (W); STABLE FLIGHT; UNSTABLE FLIGHT

V2 Thrust Power Curve

Mass of Athena v2.1 Fan: 680g
Hydrodynamic E: 0.8
ESC E: 0.8
Motor E: 0.85
Density of Air: 1.225 kg/m3
Battery Energy Denisty 180Wh/kg
Graph shows Battery Deplection to 80%
Structure Weight 4.2kg

Battery Weight (Kgs)

Condential
Geola Technologies Ltd
Neva Aerospace Ltd
March 2019

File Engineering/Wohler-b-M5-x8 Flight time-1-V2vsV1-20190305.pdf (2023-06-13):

# Flight Duration of x8 Drone using Athena v1.64 or Athena v2.2 Fans

# Flight Duration

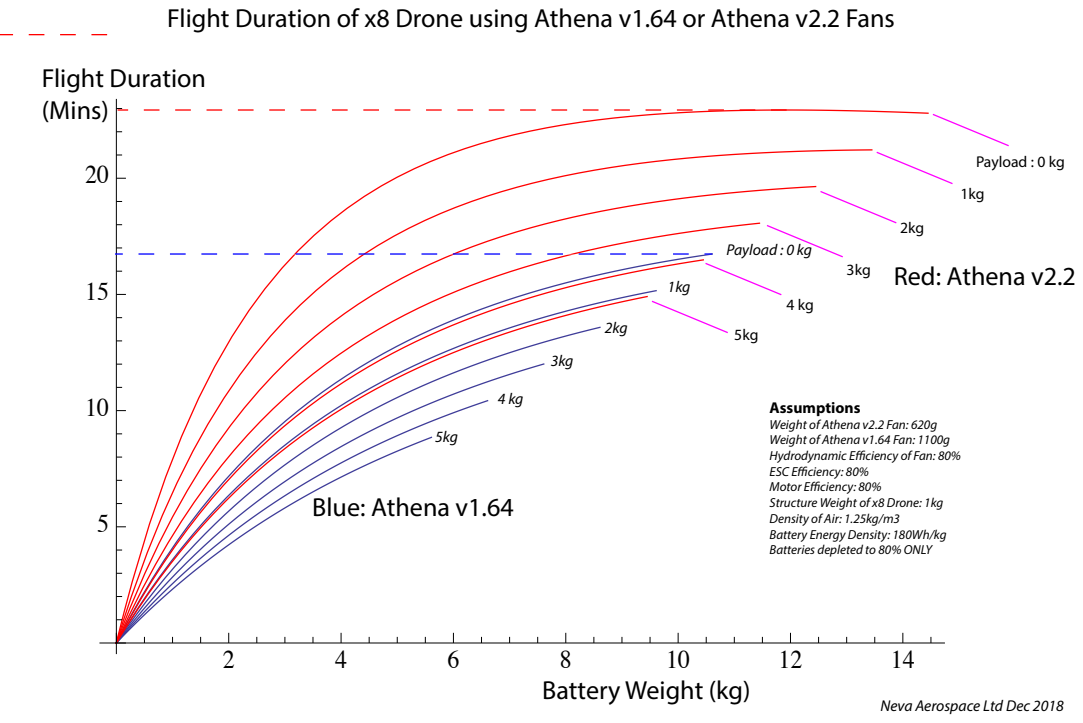
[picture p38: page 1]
(Mins); Red: Athena v2.2; Blue: Athena v1.64; Payload : 0 kg

Assumptions
Weight of Athena v2.2 Fan: 620g
Weight of Athena v1.64 Fan: 1100g
Hydrodynamic Eciency of Fan: 80%
ESC Eciency: 80%
Motor Eciency: 80%
Structure Weight of x8 Drone: 1kg
Density of Air: 1.25kg/m3
Battery Energy Density: 180Wh/kg
Batteries depleted to 80% ONLY

Battery Weight (kg)

Neva Aerospace Ltd Dec 2018

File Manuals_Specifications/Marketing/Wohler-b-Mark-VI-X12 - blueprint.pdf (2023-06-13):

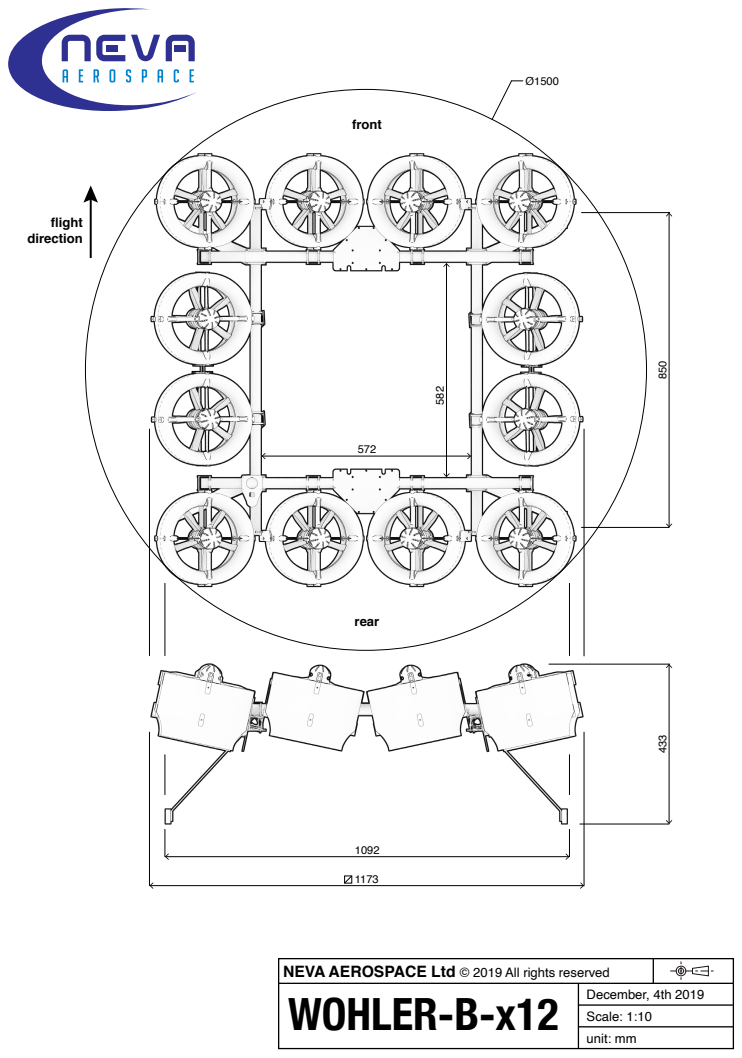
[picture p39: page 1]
rear; front; WOHLER-B-x12; December, 4th 2019; Scale: 1:10 unit: mm; flight direction

NEVA AEROSPACE Ltd © 2019 All rights reserved

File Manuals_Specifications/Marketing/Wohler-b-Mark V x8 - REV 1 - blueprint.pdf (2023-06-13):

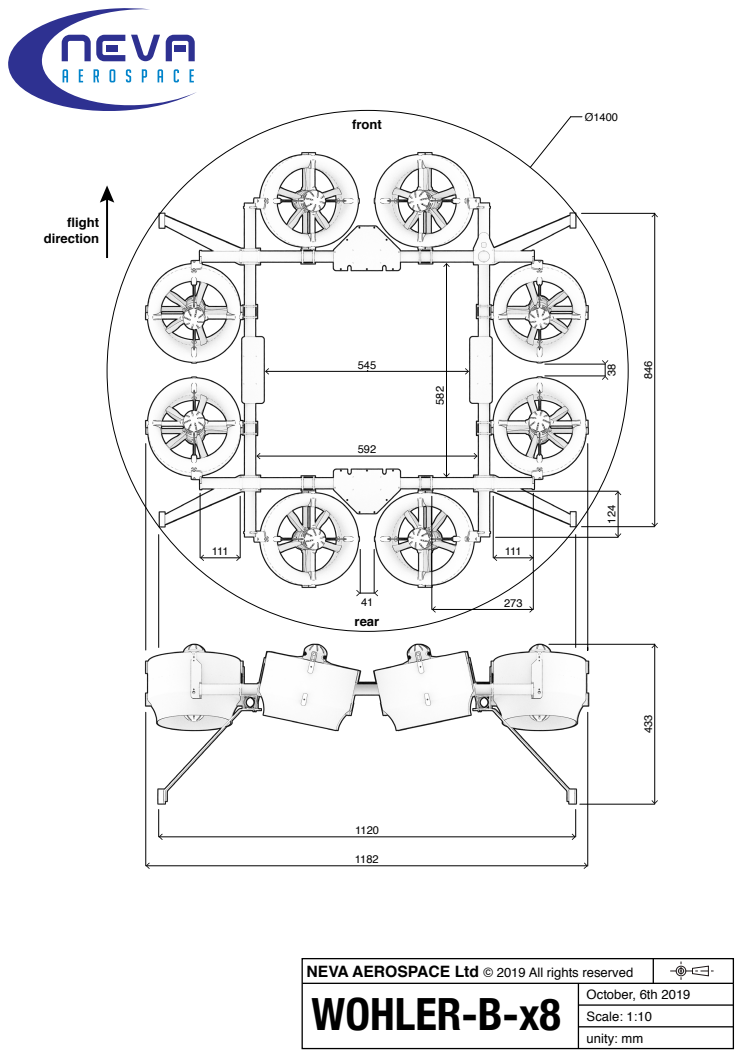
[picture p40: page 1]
WOHLER-B-x8; October, 6th 2019; rear; front; flight direction; Scale: 1:10 unity: mm

NEVA AEROSPACE Ltd © 2019 All rights reserved

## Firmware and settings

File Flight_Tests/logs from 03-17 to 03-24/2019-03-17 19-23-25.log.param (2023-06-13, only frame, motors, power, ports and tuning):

ATC_ANG_LIM_TC	1
ATC_ANG_PIT_P	3
ATC_ANG_RLL_P	3
ATC_ANG_YAW_P	3
ATC_ANGLE_BOOST	1
ATC_RAT_PIT_D	0.01
ATC_RAT_PIT_FF	0
ATC_RAT_PIT_FILT	20
ATC_RAT_PIT_I	0.3
ATC_RAT_PIT_IMAX	0.5
ATC_RAT_PIT_P	0.6
ATC_RAT_RLL_D	0.015
ATC_RAT_RLL_FF	0
ATC_RAT_RLL_FILT	20
ATC_RAT_RLL_I	0.4
ATC_RAT_RLL_IMAX	0.5
ATC_RAT_RLL_P	0.8
ATC_RAT_YAW_D	0.015
ATC_RAT_YAW_FF	0
ATC_RAT_YAW_FILT	5
ATC_RAT_YAW_I	0.15
ATC_RAT_YAW_IMAX	0.5
ATC_RAT_YAW_P	1.5
ATC_RATE_FF_ENAB	1
ATC_RATE_P_MAX	0
ATC_RATE_R_MAX	0
ATC_RATE_Y_MAX	0
BATT_AMP_OFFSET	0
BATT_AMP_PERVLT	64
BATT_CAPACITY	22000
BATT_CRT_MAH	0
BATT_CRT_VOLT	0
BATT_CURR_PIN	3
BATT_FS_CRT_ACT	0
BATT_FS_LOW_ACT	1
BATT_FS_VOLTSRC	0
BATT_LOW_MAH	0
BATT_LOW_TIMER	10
BATT_LOW_VOLT	19
BATT_MONITOR	4
BATT_SERIAL_NUM	-1
BATT_VOLT_MULT	19.027
BATT_VOLT_PIN	2
BATT2_AMP_OFFSET	0
BATT2_AMP_PERVLT	63.5927
BATT2_CAPACITY	22000
BATT2_CRT_MAH	0
BATT2_CRT_VOLT	0
BATT2_CURR_PIN	3
BATT2_FS_CRT_ACT	0
BATT2_FS_LOW_ACT	0
BATT2_FS_VOLTSRC	0
BATT2_LOW_MAH	0
BATT2_LOW_TIMER	10
BATT2_LOW_VOLT	10.5
BATT2_MONITOR	4
BATT2_SERIAL_NUM	-1
BATT2_VOLT_MULT	19.027
BATT2_VOLT_PIN	2
FLTMODE_CH	5
FLTMODE1	0
FLTMODE2	0
FLTMODE3	2
FLTMODE4	2
FLTMODE5	5
FLTMODE6	5
FRAME_CLASS	3
FRAME_TYPE	1
INS_GYRO_FILTER	20
MOT_BAT_CURR_MAX	0
MOT_BAT_CURR_TC	5
MOT_BAT_IDX	0
MOT_BAT_VOLT_MAX	26.4
MOT_BAT_VOLT_MIN	21
MOT_BOOST_SCALE	0
MOT_HOVER_LEARN	2
MOT_PWM_MAX	0
MOT_PWM_MIN	0
MOT_PWM_TYPE	0
MOT_SAFE_DISARM	0
MOT_SPIN_ARM	0.1
MOT_SPIN_MAX	0.95
MOT_SPIN_MIN	0.15
MOT_SPOOL_TIME	0.5
MOT_THST_EXPO	0.65
MOT_THST_HOVER	0.6875
MOT_YAW_HEADROOM	200
SERIAL0_BAUD	115
SERIAL0_PROTOCOL	2
SERIAL1_BAUD	57
SERIAL1_PROTOCOL	1
SERIAL2_BAUD	921
SERIAL2_PROTOCOL	1
SERIAL3_BAUD	38
SERIAL3_PROTOCOL	5
SERIAL4_BAUD	38
SERIAL4_PROTOCOL	5
SERIAL5_BAUD	57
SERIAL5_PROTOCOL	-1
SERIAL6_BAUD	57
SERIAL6_PROTOCOL	-1
SERVO1_FUNCTION	33
SERVO1_MAX	1900
SERVO1_MIN	1100
SERVO1_REVERSED	0
SERVO1_TRIM	1500
SERVO2_FUNCTION	34
SERVO2_MAX	1900
SERVO2_MIN	1100
SERVO2_REVERSED	0
SERVO2_TRIM	1500
SERVO3_FUNCTION	35
SERVO3_MAX	1900
SERVO3_MIN	1100
SERVO3_REVERSED	0
SERVO3_TRIM	1500
SERVO4_FUNCTION	36
SERVO4_MAX	1900
SERVO4_MIN	1100
SERVO4_REVERSED	0
SERVO4_TRIM	1500
SERVO5_FUNCTION	37
SERVO5_MAX	1900
SERVO5_MIN	1100
SERVO5_REVERSED	0
SERVO5_TRIM	1500
SERVO6_FUNCTION	38
SERVO6_MAX	1900
SERVO6_MIN	1100
SERVO6_REVERSED	0
SERVO6_TRIM	1500
SERVO7_FUNCTION	39
SERVO7_MAX	1900
SERVO7_MIN	1100
SERVO7_REVERSED	0
SERVO7_TRIM	1500
SERVO8_FUNCTION	40
SERVO8_MAX	1900
SERVO8_MIN	1100
SERVO8_REVERSED	0
SERVO8_TRIM	1500
SERVO9_FUNCTION	0
SERVO9_MAX	1900
SERVO9_MIN	1100
SERVO9_REVERSED	0
SERVO9_TRIM	1500

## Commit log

2023-06-13 Initial Wohler-b-Mark-V-X8
    [2019-03-17 19-23-25.log.param, 2019-03-17 19-36-37.log.param, 2019-03-18 12-25-27.log.param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]
2023-06-20 wholer further commit
    [Plate B12 - 2D drawing.dwg, Plate B12-WB5-20181212.stl, Plate C12 - 2D drawing.dwg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]
